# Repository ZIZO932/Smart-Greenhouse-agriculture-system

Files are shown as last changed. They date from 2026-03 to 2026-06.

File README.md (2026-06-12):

# Smart Greenhouse agriculture system
## Description
The Smart Greenhouse agriculture system uses a 4-layer design to protect crops like Basil from Egypt's heat and water shortages. A Raspberry Pi Pico W monitors industrial NPK and moisture sensors, then automatically triggers pumps and fans to keep everything in the perfect range. To top it off, an AI-powered camera on a circular track patrols the plants to catch diseases early.
---

## Why I Built This (The "Problem")
Farming in Egypt is genuinely getting harder. Water stress and heatwaves are a real problem, and sensitive crops like Basil and Stevia are expensive to lose. Most of the "smart farming" products I found were just monitors — they'd send you an alert saying the soil was dry, and that was it. You still had to go do something about it.
That gap is what pushed me to build this. I wanted a system that doesn't just report a problem, but fixes it. Nitrogen drops? The system pumps nitrogen. Temperature spikes? The fans come on. The whole point was to move from observation to actual automation.

---

## The 3D Model: A Three-Layer Stack
Final 3D Model

I designed this in a vertical configuration (inspired by city planning) to keep things clean and functional.

* **Layer 1 (The Pump Room):** This is the foundation. It holds a 5L main water tank for irrigation and three 1L tanks for N, P, and K nutrients. I mapped out four water pumps here, each hooked up to its own plumbing line.
* **Layer 2 (The Brain & Sensors):** This is where the electronics live. I installed industrial-grade NPK and moisture sensors here. The plumbing from the bottom passes through this layer to reach the top, which was a total nightmare to route without kinks.
* **Layer 3 (The Grow Bed):** I went with a transparent acrylic finish for the soil bed so you can actually see the root health. It uses 360-degree bubblers to make sure water reaches everywhere with zero waste.
* **The AI Track:** Encircling the top is a custom circular track. I built a small car that carries the Pi Zero and Camera, revolving around the plants every 30 minutes to catch every angle.

   **This is the link for the 3d model in step i didnt upload it here because of its size** https://drive.google.com/file/d/1caedlcHiUJ2DHqxGwvVZIDkTWpKjw0eq/view?usp=drive_link
  it is also found as a .zip file in the CAD folder

---

## Schematic & PCB Design
I spent a lot of time making sure this board wouldn't catch fire. Since the Pico is a low-power "brain," it can't handle the 12V needed for pumps and heaters.

### The Schematic
Schematic Design

The heart of the protection is the ULN2803A Darlington array. It acts as the mediator—taking tiny 3.3V signals from the Pico and using them to trigger the heavy-duty relays. I also built three distinct power rails to keep the noise down:
* **12V:** For the (pumps/fans/heaters).
* **5V:** For the MCUs (stepped down via LM2596T-5).
* **3.3V:** For the sensitive sensors (stepped down via AMS1117-3.3).

I added 560-ohm resistors and a MAX485E chip to handle the RS-485 Modbus communication with the NPK sensor. It’s industrial-grade stuff, not that cheap analog junk.

### The PCB
PCB Layout

I had to fix mistakes with relay footprints and ensure the power rails were wide enough to handle the current. I added decoupling capacitors everywhere to soak up voltage spikes from the pumps. After a few DRC (Design Rule Check), the board is officially intersection free and ready for production.

---

## AI Disease Detection
The patrol car sends images back to the Pi Zero 2W for processing. I'm training the disease detection model on the**[New Plant Diseases Dataset on Kaggle](https://www.kaggle.com/datasets/vipoooool/new-plant-diseases-dataset)**, which has a solid variety of labeled leaf conditions.
The workflow is simple: the car wakes up every 30 minutes, does one full lap around the plants scanning for spots or wilting, then returns to its dock to charge. Keeping it parked between scans was a deliberate choice to extend battery life.

---
## BOM

| Name | Cost Per Item (USD) | Quantity | Total (USD) | Link | Distributor |
| :--- | :--- | :--- | :--- | :--- | :--- |
| **Water pump** | 5.57 | 4 | 22.28 | [Link](https://www.ram-e-shop.com/shop/dc-pump-240l-water-pump12vdc-ultra-quiet-brushless-240l-h-7953) | Ram Electronics |
| **PCB Fabrication** | 5.74 | 1 | 5.74 | [Link](https://jlcpcb.com) | JLCPCB |
| **Pin Header 1x04** | 0.12 | 2 | 0.24 | [Link](https://makerselectronics.com/product/pin-headers-male-2-54mm-5pin-straight-black-11mm/) | Makers Electronics |
| **Pin Header 1x02** | 0.10 | 7 | 0.67 | [Link](https://makerselectronics.com/product/pin-headers-male-2-54mm-5pin-straight-black-11mm/) | Makers Electronics |
| **Ceramic Cap** | 0.04 | 10 | 0.38 | [Link](https://makerselectronics.com/product/ceramic-capacitor-100nf-50v/) | Makers Electronics |
| **Electrolytic Cap** | 0.10 | 4 | 0.40 | [Link](https://makerselectronics.com/product/capacitor-10uf-25v-4x7mm/) | Makers Electronics |
| **Resistor** | 0.04 | 10 | 0.40 | [Link](https://makerselectronics.com/product/carbon-resistor-10k%cf%89-2w-through-hole/) | Makers Electronics |
| **12V 5A Power Adapter** | 5.74 | 1 | 5.74 | [Link](https://makerselectronics.com/product/adapter-12v-3a-3/) | Makers Electronics |
| **Barrel Jack** | 0.29 | 1 | 0.29 | [Link](https://store.fut-electronics.com/products/dc-barrel-female-jack?_pos=2&_sid=9cbb68bec&_ss=r) | Future Electronics Egypt |
| **DIP-18 Socket** | 3.16 | 1 | 3.16 | [Link](https://store.fut-electronics.com/search?type=product&q=DIP-18+7.62mm) | Future Electronics Egypt |
| **Relay** | 1.34 | 7 | 9.38 | [Link](https://www.amazon.eg/-/en/Generic-12V-Relay-SRD-12VDC-SL-C-Automatic/dp/B09GNYCBJ8) | Amazon Egypt |
| **Schottky Diode** | 0.15 | 1 | 0.15 | [Link](https://store.fut-electronics.com/products/copy-of-diode-1n5408-3a-1000v-high-current-rectifier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) | Future Electronics Egypt |
| **Inductor** | 0.02 | 1 | 0.02 | [Link](https://makerselectronics.com/product/inductor-330uh-0510-1w/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) | Makers Electronics Egypt |
| **NPK Soil Sensor** | 61.26 | 1 | 61.26 | [Link](https://store.fut-electronics.com/products/soil-npk-nitrogen-phosphorus-potassium-nutrient-sensor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) | Future Electronics Egypt |
| **Soil Moisture Sensor** | 1.91 | 1 | 1.91 | [Link](https://www.ram-e-shop.com/shop/sen-soil-c-capacitive-analog-soil-moisture-sensor-v2-0-sku-soil-c-8116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) | RAM Electronics |
| **Light Sensor** | 3.73 | 1 | 3.73 | [Link](https://store.fut-electronics.com/products/digital-light-intensity-module) | Future Electronics Egypt |
| **Temp Sensor (air)** | 0.86 | 1 | 0.86 | [Link](https://makerselectronics.com/product/ds18b20-temperature-sensor-to-92/) | Makers Electronics Egypt |
| **Temp Sensor (soil)** | 1.63 | 1 | 1.63 | [Link](https://www.ram-e-shop.com/ar/shop/wire-ds18b20-ds18b20-waterproof-temperature-sensor-original-chip-7175) | RAM Electronics |
| **Darlington Driver** | 0.46 | 1 | 0.46 | [Link](https://makerselectronics.com/product/uln2803apg-darlington-transistor-arrays-dip-18-brand-toshiba/) | Makers Electronics |
| **RS485 Transceiver** | 0.55 | 1 | 0.55 | [Link](https://uge-one.com/product/max485-rs-485-transceiver-dip8/) | UGE Electronics Egypt |
| **Raspberry Pi Camera V2** | 15.31 | 1 | 15.31 | [Link](https://www.ram-e-shop.com/ar/shop/rpi-v2-camera-raspberry-pi-camera-module-v2-official-8-mp-hd-imx219-official-6887) | Ram Electronics |
| **LDO Regulator** | 0.06 | 1 | 0.06 | [Link](https://www.ram-e-shop.com/ar/shop/lt1117-3-3v-ams1117-3-3v-6628) | Ram Electronics Egypt |
| **Buck Converter IC** | 0.77 | 1 | 0.77 | [Link](https://makerselectronics.com/product/lm2596t-5-0-buck-fixed-40v-5v-3a-to-220-5l-dc-dc-converters-dip-ic/) | Makers Electronics Egypt |
| **Raspberry Pi Zero 2W** | 38.28 | 1 | 38.28 | [Link](https://devboardsmarket.com/products/raspberry-pi-zero-2-w) | DEV boards |
| **Raspberry Pi Pico W** | 16.27 | 1 | 16.27 | [Link](https://www.ram-e-shop.com/ar/shop/rpi-pico-w-raspberry-pi-pico-w-wifi-8524) | RAM electronics |
| **GRAND TOTAL** | | | **$189.94** | | |

## The Build: From CAD to Reality

After the design got approved, it was time to build the prototype — and as always, the real world had different plans than the 3D model.



The body is built from MDF wood with a polyethylene cover for the grow layer. First attempt used nails, which couldn't hold the weight and the frame fell apart — switched to screws and it held solid after that. Pumps and tubing were routed through the layers down to the soil bed.

Circuit

For the circuit, I soldered up the power supply (3.3V/5V step-downs, 10A fuse), wired in the sensors (BH1750, DS18B20, NPK via RS-485/MAX485) and the relay module driving the pumps, fans, Peltier module, and LEDs. Fried a Pico along the way and switched to an ESP32.

Dashboard

Real-time data flows through MQTT (Mosquitto) into a web dashboard built with HTML/CSS/JS and Grafana, showing live sensor readings against the ideal ranges for sweet basil.

Ran a full 6-hour test with everything powered on together — sensors reading correctly, pumps responding properly, and all values staying within range. The Smart Greenhouse Agriculture System is built and working. 🌱

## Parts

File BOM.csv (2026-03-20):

Name | Purpose | Cost Per Item (USD) | Quantity | Total (USD) | Link | Distributor
Water pump | to pump water and solution to irrigate the soil and plant | 5.57 | 4 | 22.28 | https://www.ram-e-shop.com/shop/dc-pump-240l-water-pump12vdc-ultra-quiet-brushless-240l-h-7953 | Ram Electronics
PCB Fabrication | to mount components | 5.74 | 1 | 5.74 | https://jlcpcb.com | JLCPCB
Pin Header 1x04 | To connect pico with zero | 0.12 | 2 | 0.24 | https://makerselectronics.com/product/pin-headers-male-2-54mm-5pin-straight-black-11mm/ | Makers Electronics
Pin Header 1x02 | To connect pico with zero | 0.10 | 7 | 0.67 | https://makerselectronics.com/product/pin-headers-male-2-54mm-5pin-straight-black-11mm/ | Makers Electronics
Ceramic Cap | circuit | 0.04 | 10 | 0.38 | https://makerselectronics.com/product/ceramic-capacitor-100nf-50v/ | Makers Electronics
Electrolytic Cap | circuit | 0.10 | 4 | 0.40 | https://makerselectronics.com/product/capacitor-10uf-25v-4x7mm/ | Makers Electronics
Resistor | For the circuit | 0.04 | 10 | 0.40 | https://makerselectronics.com/product/carbon-resistor-10k%cf%89-2w-through-hole/ | Makers Electronics
12V 5A Power Adapter | to power the whole system | 5.74 | 1 | 5.74 | https://makerselectronics.com/product/adapter-12v-3a-3/ | Makers Electronics
Barrel Jack | to plug in the 12V power supply | 0.29 | 1 | 0.29 | https://store.fut-electronics.com/products/dc-barrel-female-jack?_pos=2&_sid=9cbb68bec&_ss=r | Future Electronics Egypt
DIP-18 Socket | Holds the ULN2803A chip so you can replace it easily | 3.16 | 1 | 3.16 | https://store.fut-electronics.com/search?type=product&q=DIP-18+7.62mm | Future Electronics Egypt
Relay | switches that allow the Pico (low power) to turn on the Water Pumps, Fan, and Heater (high power) | 1.34 | 7 | 9.38 | https://www.amazon.eg/-/en/Generic-12V-Relay-SRD-12VDC-SL-C-Automatic/dp/B09GNYCBJ8 | Amazon Egypt
Schottky Diode | parts of the buck converter circuit | 0.15 | 1 | 0.15 | https://store.fut-electronics.com/products/copy-of-diode-1n5408-3a-1000v-high-current-rectifier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 | Future Electronics Egypt
Inductor | parts of the buck converter circuit | 0.02 | 1 | 0.02 | https://makerselectronics.com/product/inductor-330uh-0510-1w/ | Makers Electronics Egypt
NPK Soil Sensor | To monitor the NPK in soil (nitrogen, phosphorus, potassium) | 61.26 | 1 | 61.26 | https://store.fut-electronics.com/products/soil-npk-nitrogen-phosphorus-potassium-nutrient-sensor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 | Future Electronics Egypt
Soil Moisture Sensor | To monitor the soil moisture | 1.91 | 1 | 1.91 | https://www.ram-e-shop.com/shop/sen-soil-c-capacitive-analog-soil-moisture-sensor-v2-0-sku-soil-c-8116 | RAM Electronics
Light Sensor | To monitor the light intensity | 3.73 | 1 | 3.73 | https://store.fut-electronics.com/products/digital-light-intensity-module | Future Electronics Egypt
Temp Sensor (air) | To monitor the temp of air in the greenhouse system | 0.86 | 1 | 0.86 | https://makerselectronics.com/product/ds18b20-temperature-sensor-to-92/ | Makers Electronics Egypt
Temp Sensor (soil) | To monitor the temp of soil | 1.63 | 1 | 1.63 | https://www.ram-e-shop.com/ar/shop/wire-ds18b20-ds18b20-waterproof-temperature-sensor-original-chip-7175 | RAM Electronics
Darlington Driver | lets the Pico's tiny signal actually trigger the heavy coils inside the relays | 0.46 | 1 | 0.46 | https://makerselectronics.com/product/uln2803apg-darlington-transistor-arrays-dip-18-brand-toshiba/ | Makers Electronics
RS485 Transceiver | Translates the industrial signal from the NPK sensor into a language the Pico | 0.55 | 1 | 0.55 | https://uge-one.com/product/max485-rs-485-transceiver-dip8/ | UGE Electronics Egypt
Raspberry Pi Camera Module V2 | The eyes for the Pi Zero for ai. | 15.31 | 1 | 15.31 | https://www.ram-e-shop.com/ar/shop/rpi-v2-camera-raspberry-pi-camera-module-v2-official-8-mp-hd-imx219-official-6887 | Ram Electronics
LDO Regulator | power regulates down the voltage to a 3.3V rail | 0.06 | 1 | 0.06 | https://www.ram-e-shop.com/ar/shop/lt1117-3-3v-ams1117-3-3v-6628 | Ram Electronics Egypt
Buck Converter IC | To step down the voltage. | 0.77 | 1 | 0.77 | https://makerselectronics.com/product/lm2596t-5-0-buck-fixed-40v-5v-3a-to-220-5l-dc-dc-converters-dip-ic/ | Makers Electronics Egypt
Raspberry Pi Zero 2W | It would be used in the AI disease detection using pi camera | 38.28 | 1 | 38.28 | https://devboardsmarket.com/products/raspberry-pi-zero-2-w | DEV boards
Raspberry Pi Pico W | The main controller for the sensors and actuators | 16.27 | 1 | 16.27 | https://www.ram-e-shop.com/ar/shop/rpi-pico-w-raspberry-pi-pico-w-wifi-8524 | RAM electronics

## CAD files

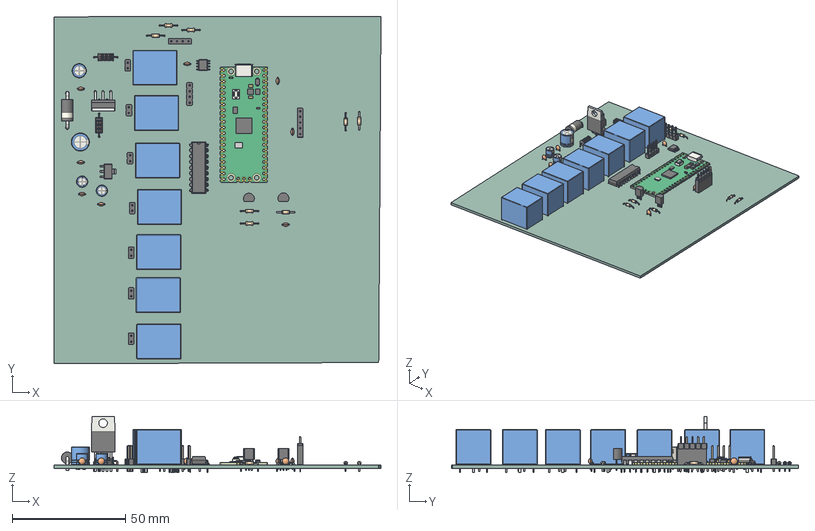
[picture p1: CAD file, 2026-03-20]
CAD/cap 204.step
144.5 x 153.5 x 24.8 mm
C_Disc_D3.0mm_W1.6mm_P2.50mm x 8
R_Axial_DIN0204_L3.6mm_D1.6mm_P7.62mm_Horizontal x 8
D_DO-201AD_P15.24mm_Horizontal
Relay_SPDT_SANYOU_SRD_Series_Form_C x 7
PinHeader_1x05_P2.54mm_Vertical
PinSocket_1x05_P2.54mm_Vertical
SOIC-8_3.9x4.9mm_P1.27mm
PinHeader_1x02_P2.54mm_Vertical x 7
RaspberryPi_Pico_Module_KiCad
SOT-223
TO-92_Inline x 2
PinHeader_1x04_P2.54mm_Vertical x 2
L_Axial_L7.0mm_D3.3mm_P10.16mm_Horizontal_Fastron_MICC x 2
CP_Radial_D5.0mm_P2.50mm x 2
CP_Radial_D6.3mm_P2.50mm
TO-220-5_P3.4x3.7mm_StaggerOdd_Lead3.8mm_Vertical
DIP-18_W7.62mm
CP_Radial_D8.0mm_P3.50mm
cap 204_PCB

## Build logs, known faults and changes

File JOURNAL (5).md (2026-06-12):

<!--
  This journal is auto generated by Stasis.
-->

# 6/12/2026 6 PM - Final Day

_Time spent: 6h_

Today was the final push. I mounted the ESP32 and the relay module inside the electronics layer and connected everything back to the circuit I had built in the first four days. I also attached the LED strip to the inner roof and mounted the Peltier module and fan on the upper wall. After everything was physically in place I powered it on for the first time as a complete system and it actually worked which was a relief. The sensors were reading correctly and the pumps were responding to the relay signals. I ran a quick test by letting it run for a couple hours while I watched the readings on the webpage and everything stayed in range. The prototype is done. And i did a full test plan video in which it worked for full 6 hours.

image (2)

image (1)




# 6/12/2026 6 PM - Construction Day 2 Prototype fix

_Time spent: 5h_

Today was probably the worst day so far. When I was moving the prototype to test the fit of the layers, the whole thing basically fell apart because the nails couldn't handle the weight. I had to stop everything and rethink the joining method. I replaced all the nails with screws which required drilling holes first which took a lot of time but the structure became way more solid after that. I also started mounting the pumps on the top layer and routing the silicone tubing down through the layers to the soil bed. Getting the tubes to go through without kinking was a pain but I figured it out by the end.











# 6/12/2026 6 PM - Construction Day 1

_Time spent: 4h_

Today I started the actual construction of the body. I began by cutting the MDF wood into the right dimensions for the walls and the layers. It took more time than I expected since I had to measure everything twice to make sure the layers would actually line up. After cutting, I started assembling the frame using nails and wood glue to hold everything together. It looked solid at first but I had a feeling the nails weren't going to hold for long since the wood pieces were pretty heavy. I also cut the polyethylene sheet and attached it to the upper layer to act as the greenhouse cover. Getting it tight and wrinkle free was annoying but I managed. At the end of the day the basic skeleton of the prototype was standing which felt good.











# 6/12/2026 6 PM - Website

_Time spent: 4h_

Today, I began making my webpage. I used the Grafana JS library, and I used basic HTML, CSS, and JS. I wrote the code to illustrate a real-time graph from phpMyAdmin. And I wrote the perfect conditions for our plant, which is sweet basil. Also, I made its style like our poster for the project, and I made it read the signals from the ESP using Wi-Fi, and I took a lot of time to make it. Since there were some mistakes in the code, like a bad connection or bad signal, I took some time to figure it out, but I corrected the code, and it worked at the end.

web_1

web_2

web_3





# 6/12/2026 6 PM - ESP Server

_Time spent: 5h_

Today, I wanted to make a server to provide the readings and the real-time graphs to my website, which I will build. I began by searching for popular protocols that can be used with the ESP32. I found that the best IoT-based protocol is MQTT. I installed Mosquitto, which is a really fast and reliable server to host my client. I had some problems when I was using it, so I began researching, and I changed some lines in mosquitto.config. Also, I installed XAMPP to serve my web page on the World Wide Web and to be the main server to run Apache and MySQL, and I wrote Python code to connect my ESP32 signals with Grafana from my web page to display real-time graphs. This is the code I wrote [python 1, python 2 images]. Also, I wrote an MQTT code to test my prototype as shown in these images [mqtt 1, mqtt 2].

python_1

python_2

mqtt_1

mqtt_2






# 6/12/2026 6 PM - Circuit Day 2

_Time spent: 3h_

On day two I began by wiring up the relay, ESP32, temp sensor (DS18B20), and light sensor (BH1750) and began connecting the RS485 NPK sensor. Also, I connected the MAX485 to be the main translator between the ESP32 and the NPK sensor. It took some time since it needed a 4800 baud rate and needed 12 volts, so I wired the power supply too, and the NPK sensor was hard to code, and I took like an hour to make it work.
Until now, I didn’t check the capacitors of all the sensors and some of the actuators since I had a deadline and exams in school. So I remade their systems again, but a lot faster now, and all worked by a simple code that was testing everything on its own. Then when I connected all of them, there was an overload on the step-down LM35, which was burnt. Also, I didn’t begin in the logic till now, but the light sensor was not working properly and had many wrong measures, and then I rewired the connections and reuploaded the code; it worked.











# 6/12/2026 6 PM - Circuit Day 1

_Time spent: 6h_

On day one, I started working on the circuit; I reviewed the schematic and confirmed that all the components I had purchased were present. Then I began by soldering the Pico. Then I soldered some more components. After that, I began connecting the power supply and the switch, which was the essential part for the project since it is the main power source as shown in this image. It took me some time to figure out that we needed a 10 amp fuse, so we got it, and it worked, and we measured it using a multimeter. After that, I connected the circuit of the power supply to reduce noise, and I connected the AMS1117 and LM25, which are step-downs, one for 3.3 volts and the other for 5 volts.
After that we got the breadboard and added the Pico to it. Then I connected the Pico with 5V from the power supply, so I fried it literally. I had an old ESP32, and when we checked, we used it instead of the Pico and connected it correctly with the power supply using a step-down, obviously. Then I began connecting the components into the breadboard. I connected the DS18B20 temp sensor and the BH1750, but I had a problem with the BH1750, which was that I connected it with the power supply, and I figured out that it should be connected to the 3.3V from the ESP32. It took me like 15 minutes to figure that out.
I began connecting the relay module, and I had trouble knowing if it was high-based or low-based, which makes the code different, so I know it is high-based, and also I began connecting the actuators like the water pumps, fans, Peltier module, and LEDs. At first it didn’t work at all since I was connecting it to 5 volts instead of 12 volts, so I reconnected it, and I made sure that everything was working and the signals were correctly matching the channels of the relay module.
WhatsApp Image 2026-04-19 at 2.10.47 PM






# 3/19/2026 12 PM - Building the Firmware last day

_Time spent: 3h_

Today I worked on the Pi Zero communication code, using UTF-8 to make sure everything reads correctly and keeping it all in JSON format so the data stays organized. I also built an NPK alert system to catch any big nutrient problems before they cause damage. After that, I added the specific functions for the water pumps, fans, and heaters to control them based on what the sensors are actually seeing. I made sure to include an emergency function too, just so I have a quick way to shut down all the actuators at once if something goes wrong.

This was the last day for the firmware since I finally got into the main.py file. I started with a simple welcome message and declared all my variables. The main while loop is now running—it reads through the sensors one by one, checks the Pi Zero connection, and sends the data over. I added a 500ms delay at the end to keep the timing stable. To wrap things up, I made a keyboard interrupt function so I can kill the whole process and close every relay instantly if I need to stop the system manually.






















# 3/18/2026 12 PM - Building the Firmware 1

_Time spent: 4h_

This was the firs day in which I started on the firmware for the project. I began by setting up the optimal values for the Basil plants, putting all the min and max parameters into one class. I also made a separate class to define what every pin on the Pico actually does so the code stays organized.

For the sensors, I started with the BH1750 light sensor. I wrote the code to check the I2C connection, handle the read delays, and then I used a formula I found to convert the raw data into actual light levels. Next, I worked on the NPK sensor, which has 7 registers. I built a function for it to self-read and return the soil nutrient data.

After the sensors, I moved on to the relays. I wrote functions to handle opening, closing, and timing for each one. For the temperature sensors, I used the OneWire library to scan the DS18B20 sensors. I set them to 12-bit conversion for better accuracy and added an "if" condition to sort the readings between soil and air temperature.

The moisture sensor was simpler since it just reads the data directly. Finally, I coded the light schedule to manage the plant's day/night cycles, which is pretty important for the photosynthesis and respiration process.

















# 3/17/2026 12 PM - AI Tracking System

_Time spent: 2h_

I finally got the physical model for the tracking system done. I designed a circular track that runs along the perimeter of the top layer to give the camera a full view of the plants. I also built a small car that sits on this track to carry the Raspberry Pi Zero 2W and the Pi Camera.

The idea is for the car to revolve around the growing area so it can catch every angle of the plants. I made sure the car is stable enough to hold the electronics and the battery pack while it moves. It took some time to get the curves of the track right so the car wouldn't get stuck, but it’s now a smooth loop. This setup is what will allow the AI to scan for diseases every 30 minutes before returning to its home position to save power.


















# 3/16/2026 12 PM - PCB Design and footprint

_Time spent: 5h_

Today, I began mapping my pcb design and preparing the footprints for the sensors and actuators. And I began with connecting each part like the RS485 sensors and capacitors and every sensors as a different system. Which take some time. I faces some problem which is the capacitors was different sizes and I didn't see that so I searched on every capacitor and its footprints.then by connecting the main power rails for every system and made sure every thing is connected without intersections. Also, I made sure to connect everything with it's rails. I connected the relays system and discovered I made a mistake in the footprints of the relays and I searched on the true ones and I made them and reconnected the relays systems. So, I ran a DRC check and found some errors like the silicon pring and the edge cuts. And some pins which is not allained with the schematic of the pi pico. So I got the true footprints and reconnected the system again and made made sure every thing is connected the right way and ran another DRC every thing was working.












# 3/15/2026 12 PM - High-Power Actuators with a Low-Power Brain

_Time spent: 4h_

Today was all about the "muscles" of the system, getting the ULN2803A Darlington array wired up. Think of it as the mediator between the Raspberry Pi Pico and the Relay Modules. Since the Pico is a low-power "brain," it doesn't have the strength to flip the heavy-duty switches (the relays) that control my water pumps, fans, and heaters. The ULN2803A acts as the driver that allows those tiny 3.3V signals to trigger the high-power actuators without blowing anything up.

I spent the rest of the day in a deep-focus wiring marathon, connecting the sensors to the Pico. This wasn't just plug-and-play; I had to add the specific capacitors and resistors for each sensor to keep the data lines clean and protected. The real puzzle was the pin mapping, I had to go through the datasheets one by one to make sure every sensor's specific protocol (like I2C or Analog) was matched to a compatible pin on the Pico. It was a lot of double-checking, but the core "control center" is finally wired and ready to talk to the environment.

















# 3/14/2026 12 PM - Bridging the Pico and the Pi Zero

_Time spent: 5h_

This phase of the schematic was all about the "handshake" between the different brains of the system. After spending yesterday hunting down the exact libraries and PCB footprints for my components, I finally got everything imported and verified. Today’s mission was power and communication: getting the Raspberry Pi Pico and the Pi Zero 2W wired up to the same power rails and linked together. Since the Pi Zero will be moving on that circular track around the plants (rather than sitting on the main board), I designed header pins into the schematic so I can easily plug it in via a ribbon cable or jumper wires.

The real technical hurdle was the RS-485 communication. I integrated a MAX485E to act as the translator between the Pico’s logic and the industrial NPK sensor. Since the sensor runs on 12V, I tapped into the high-voltage rail, but I had to be careful with the signal lines. I used 560-ohm resistors to bias the lines and manage the charge so it’s perfectly safe for the MAX485 and the Pico to handle.

I also threw in a dedicated decoupling capacitor for the MAX485 chip itself; it’s a small detail, but it’s there to soak up any voltage spikes or "kickback" when the power gets cut, ensuring I don’t fry my communication bridge. It’s starting to look like a real industrial controller now.

















# 3/13/2026 12 PM - Staring Schematic

_Time spent: 3h_

Today was all about diving into the schematic design, which turned out to be a lot more about "protection" than just making connections. After doing some digging, I realized that every MCU and IC is actually pretty fragile—they need specific capacitors and resistors just to survive voltage spikes or prevent short-circuit damage. It’s one of those things you don't think about until you realize a tiny spark could fry your whole project.

To keep things organized, I mapped out three distinct power rails: 12V for the heavy-duty actuators, 5V for the MCUs, and 3.3V for the more sensitive sensors. Having these rails makes the wiring way less of a headache. I’m using a single 12V adapter as the main heart of the system, then stepping it down using an LM2596T-5 for the 5V line and an AMS1117-3.3 for the 3.3V line.

I didn't want to take any chances with stability, so I added four capacitors to each regulator to smooth out the voltage and act as a tiny buffer if the power flickers. I also integrated an inductor with the LM2596 to cut down on energy loss and threw in a diode to make sure current doesn't accidentally flow backward and wreck the source. It’s a lot of extra components, but it’s the only way to make sure the "brain" of the system doesn't lose its mind the second a pump kicks in. 












# 3/12/2026 12 PM - AI disease detection

_Time spent: 3h_

I also came up with a pretty ambitious plan for an AI disease detection subsystem to sit right on top of everything. The idea is to have a Raspberry Pi Zero 2W and a Pi Camera Module mounted on a wheeled platform that actually travels along a circular track around the perimeter of the growing area in Layer 3. This way, instead of a static view, the camera revolves around the plants to catch every single angle from a consistent distance.

To keep it efficient, the plan is for the system to run on a 30-minute cycle: every half hour, the platform wakes up, completes a full loop to capture images of the plants, and then returns to its home position to power down the motors completely. It’s designed to be a totally independent circuit from the main monitoring board, but it will feed all its visual data into the same cloud. I haven't built the physical model for this part yet, but having the concept mapped out gives me a clear path for adding high-tech "eyes" to the setup later on. The first image shows raspberry pi zero 2w connected to pi camera. and for the second image i got it from a research that trained an ai model to detect diseases.












# 3/11/2026 12 PM - Layer 2 and 3

_Time spent: 5h_

It took some serious effort, but I finally finished the three-layer stack. After the pump layer was set, I moved on to the second level, which acts as the brain for the electronics and sensors. The real grind was making sure the pipes from the bottom pumps were actually routed and connected properly to the bubblers on top without any kinks. Once the plumbing was secure, I installed the NPK and moisture sensors into the second layer, carefully positioning them so they’d be fully submerged in the soil once the bed was filled.

For the final layer, I went with a transparent acrylic finish for the soil bed so I can actually see the root health and water flow from the outside. Getting all three layers to line up, pumps on the bottom, sensors in the middle, and soil on top, was a massive coordination task, but seeing it all stacked together with the bubblers in place makes the whole system feel real. These are some figures of the whole model till now.













# 3/10/2026 12 PM - Layer 1

_Time spent: 1.5h_

I started the 3D model by setting up Layer 1 and getting the plumbing foundation right. It actually took me quite a while just to track down the exact 3D models I needed to match my parts, but once I had them, I mapped out the base and installed the four water pumps. I connected each one to its own tank, one 5-liter main tank for irrigation and three 1-liter tanks for the N, P, and K nutrients, and made sure every pump was properly hooked up to its own pipe. It’s a clean setup, and now that the physical layout is finished, the first layer is officially ready. i attached two pictures of the model.












# 3/9/2026 12 PM - Actuators selection

_Time spent: 4h_

After the sensors selection i shifted my focus on the actuators. My goal was simple on paper but a nightmare in practice: build a dedicated correction system for every single parameter I’m monitoring.

For the soil, I mapped out a 5-liter main water tank with a water pump for basic irrigation. But the NPK part is where it got complicated; I decided to add three separate pumps to dose Nitrogen, Phosphorus, and Potassium independently based on what the sensors say. I also found that to irrigate with least loss in water i need a 360 degree bubbler which i found in multiple websites.

For the climate, I settled on a fan and a heater to lock the temperature between 25°C and 30°C, plus a high-output LED. 

With 4 sensors and 7 actuators, I needed a controller that could handle a lot of I/O. I chose the Raspberry Pi Pico W. I love the Pico for its speed, and the "W" version gives me the Wi-Fi I’ll eventually need for a real-time feedback dashboard. The struggle today was mapping the pins. I realized that the Pico’s 3.3V logic can't directly talk to 12V pumps or the RS-485 sensor.
In the first image it shows the bubbler i want to use where to irrigate the whole soil i needed 360 one that has high reach.
In the second image it shows the schematic of a smart greenhouse system in which i took the idea of using a pico. 












# 3/8/2026 12 PM - Solution parameters and sensors selection

_Time spent: 5h_

Today i struggled in choosing parameters in the end i chose : NPK, Temperature, Light, and Soil Moisture. I figured if I could actually control these variables, I could grow high-value stuff like Basil or Stevia basically anywhere. Once I had the plan, I needed the "eyes" of the system and that’s where the real headache started. I spent hours looking for soil sensors, only to realize most of the cheap ones are basically toys; they just give you a vague conductivity reading and can't tell Nitrogen from Potassium.
I finally found an industrial RS-485 Modbus RTU NPK sensor. It’s way more expensive, and I know the code is going to be a total nightmare compared to a simple analog sensor, but it actually gives me real data i wanted. I also grabbed a capacitive moisture sensor because I knew the standard resistive ones would just rust and die in the soil. At least now I know the hardware can actually handle the job. The first image shows the NPK sensor i chose where its a bit expensive compared to something like 7 in 1 sensor the problem is the accuracy in which i want to make sure that the plant wont die not just a theortical thingy.
The second image is an image of the module used to connect the NPK sensor to any microcontroller. The third image shows the moisture soil sensor that was chosen due to the covarge of its forks which prevents rust.


















# 3/7/2026 12 PM - The Problem and past solutions

_Time spent: 4h_

For the first day it was all about the "Problem Selection" phase for my Capstone. I can't just build something "cool" it has to solve a legitimate Egyptian challenge. I spent hours looking into the agricultural sector. Egypt is struggling with environmental instability and major water stress. High-value aromatic crops like **Basil and Stevia** are taking a hit because they are so sensitive to heatwaves and irregular irrigation.

The Struggle i faced when searching for solutions is that Most smart pots only monitor; they don't fix. I realized I needed a system that actually manioulate the environment.
The Solution i chose was A 4-layered vertical infrastructure. It mimics city planning in which (Water pumbs and tank - Electronics - Soil - Environment). The first image shows a figure that i found in this paper (Smart Greenhouse Automation
System) where they developed the system in layers to make it easy to bulid and modify.
In the second image i attached there was the process that the system works in.













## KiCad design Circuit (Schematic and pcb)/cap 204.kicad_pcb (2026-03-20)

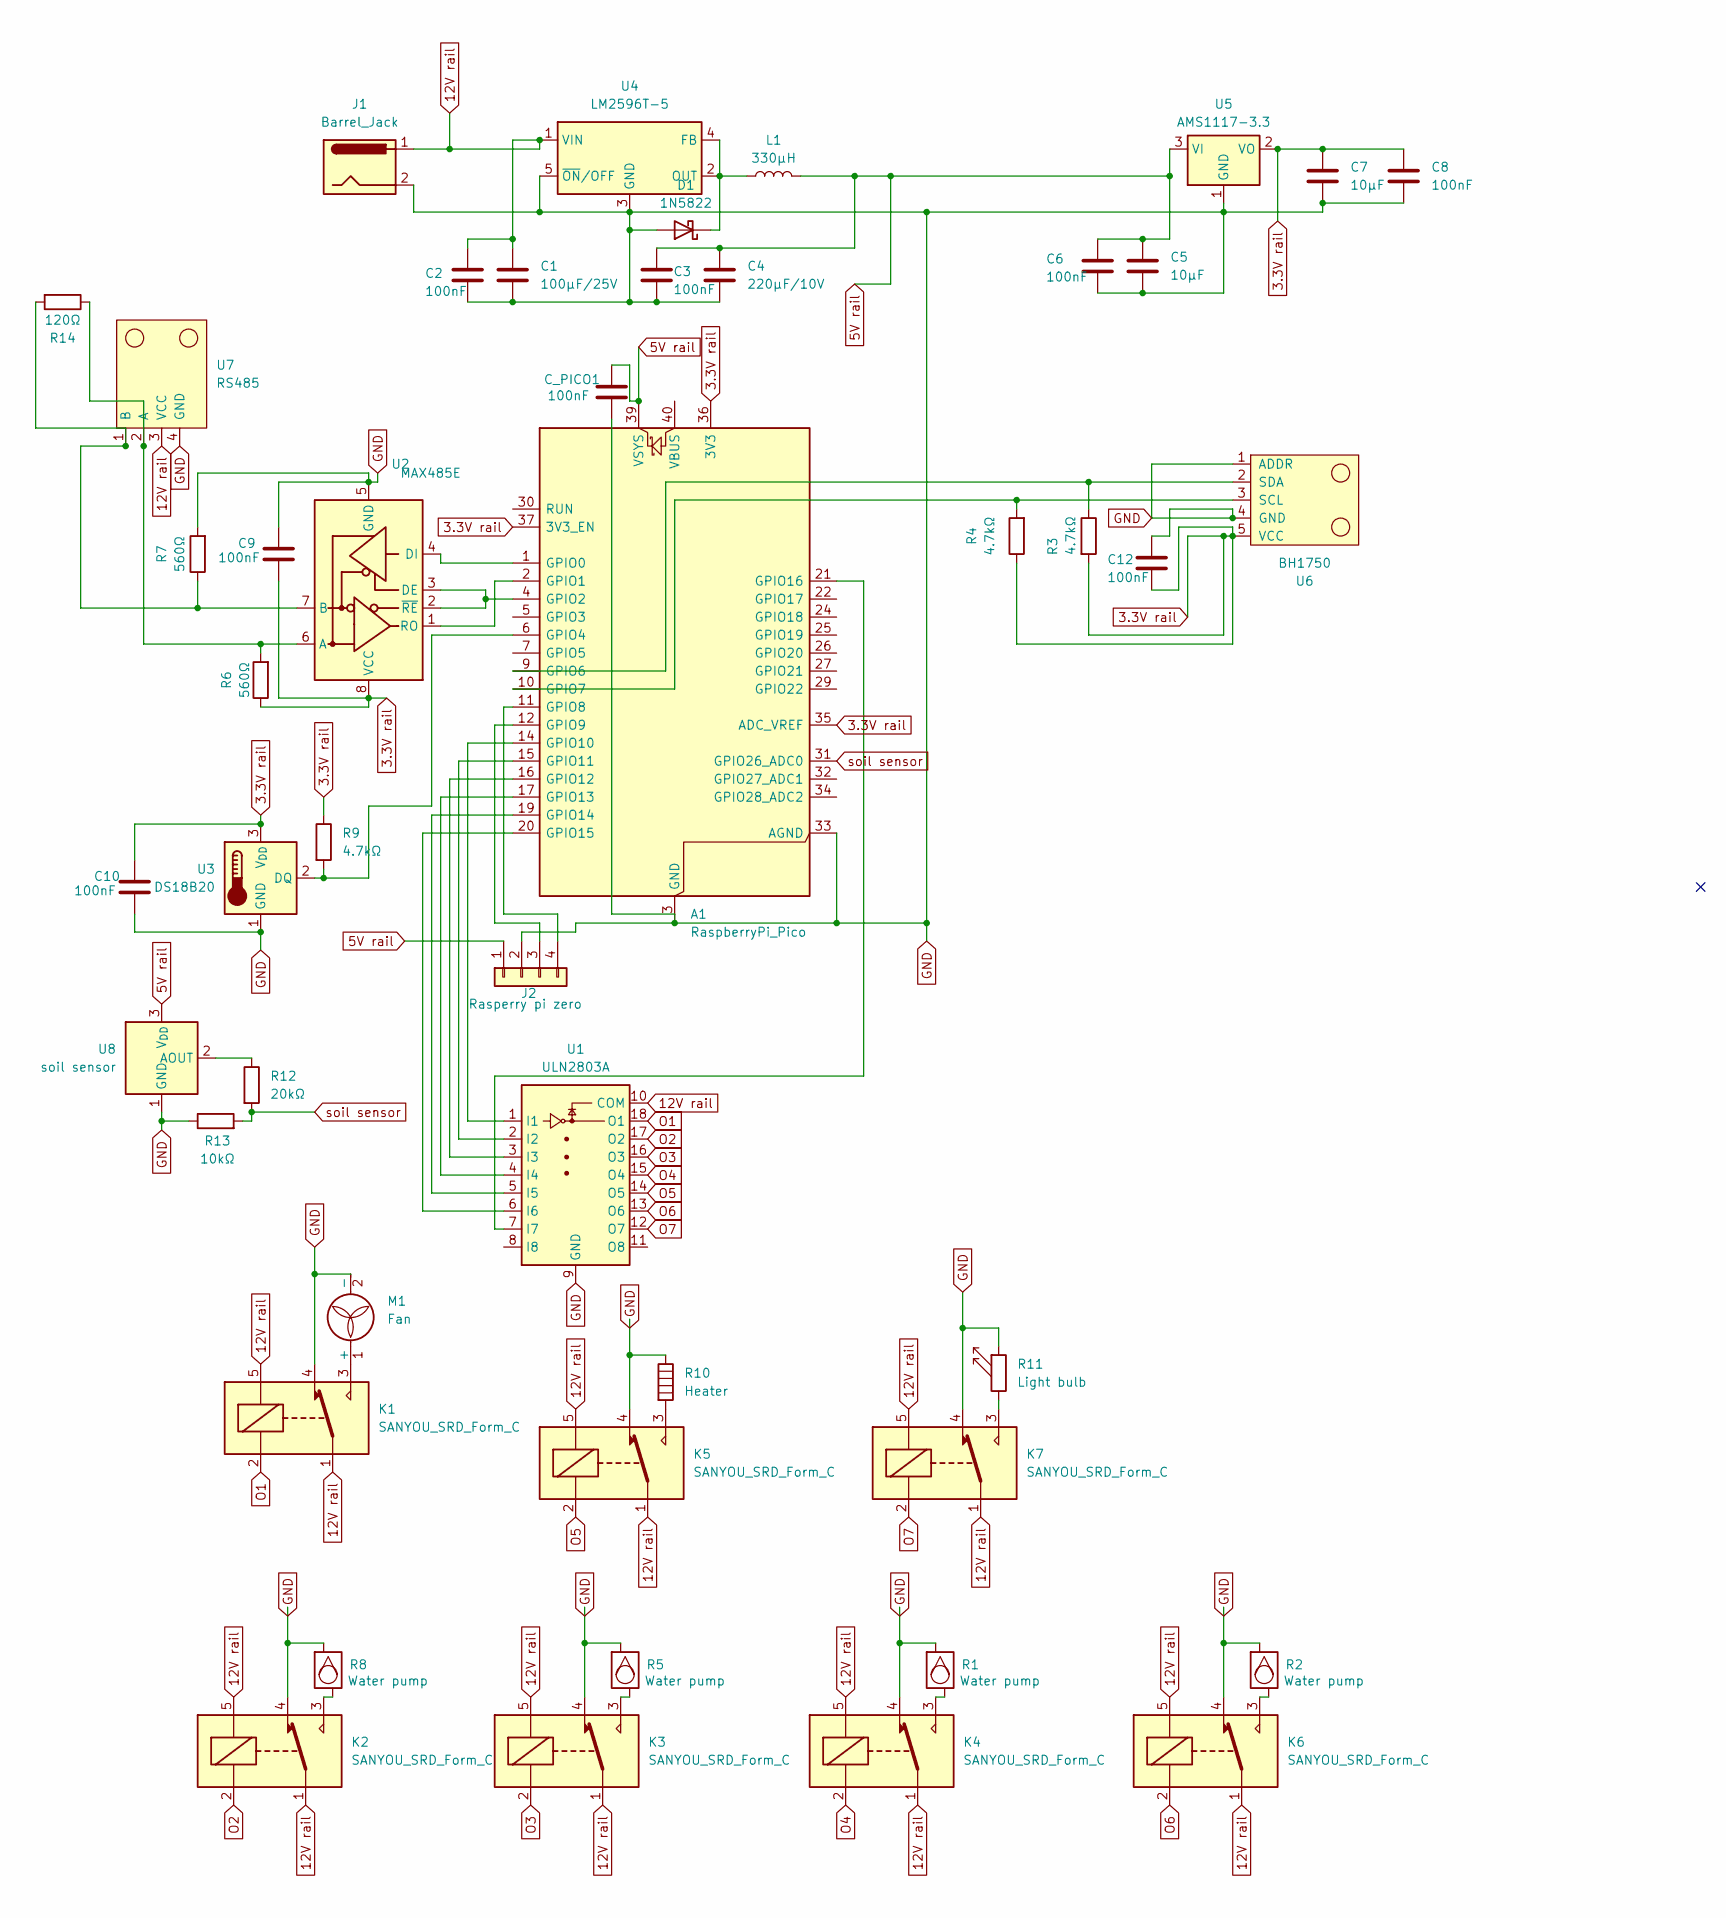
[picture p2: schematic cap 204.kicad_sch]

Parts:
A1: RaspberryPi_Pico; RaspberryPi_Pico_Common_Unspecified
C1: 100µF/25V; CP_Radial_D6.3mm_P2.50mm
C2, C3, C6, C8, C9, C10, C12: 100nF; C_Disc_D3.0mm_W1.6mm_P2.50mm
C4: 220µF/10V; CP_Radial_D8.0mm_P3.50mm
C5, C7: 10µF; CP_Radial_D5.0mm_P2.50mm
C_PICO1: 100nF; C_Disc_D3.0mm_W1.6mm_P2.50mm
D1: 1N5822; D_DO-201AD_P15.24mm_Horizontal
J1: Barrel_Jack; L_Axial_L7.0mm_D3.3mm_P10.16mm_Horizontal_Fastron_MICC
J2: Rasperry pi zero; PinHeader_1x04_P2.54mm_Vertical
K1, K2, K3, K4, K5, K6, K7: SANYOU_SRD_Form_C; Relay_SPDT_SANYOU_SRD_Series_Form_C
L1: 330µH; L_Axial_L7.0mm_D3.3mm_P10.16mm_Horizontal_Fastron_MICC
M1: Fan; PinHeader_1x02_P2.54mm_Vertical
R1, R2, R5, R8: Water pump; PinHeader_1x02_P2.54mm_Vertical
R3, R4, R9: 4.7kΩ; R_Axial_DIN0204_L3.6mm_D1.6mm_P7.62mm_Horizontal
R6, R7: 560Ω; R_Axial_DIN0204_L3.6mm_D1.6mm_P7.62mm_Horizontal
R10: Heater; PinHeader_1x02_P2.54mm_Vertical
R11: Light bulb; PinHeader_1x02_P2.54mm_Vertical
R12: 20kΩ; R_Axial_DIN0204_L3.6mm_D1.6mm_P7.62mm_Horizontal
R13: 10kΩ; R_Axial_DIN0204_L3.6mm_D1.6mm_P7.62mm_Horizontal
R14: 120Ω; R_Axial_DIN0204_L3.6mm_D1.6mm_P7.62mm_Horizontal
U1: ULN2803A; DIP-18_W7.62mm
U2: MAX485E; SOIC-8_3.9x4.9mm_P1.27mm
U3: DS18B20; TO-92_Inline
U4: LM2596T-5; TO-220-5_P3.4x3.7mm_StaggerOdd_Lead3.8mm_Vertical
U5: AMS1117-3.3; SOT-223-3_TabPin2
U6: BH1750; module_bh1750
U7: RS485; PinHeader_1x04_P2.54mm_Vertical
U8: soil sensor; TO-92_Inline

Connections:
3.3V rail: A1.35 (ADC_VREF), A1.36 (3V3), A1.37 (3V3_EN), C7.1, C8.1, C9.2, C10.1, C12.2, R3.2, R4.1, R6.1, R9.1, U2.8 (VCC), U3.3 (V_{DD}), U5.2 (VO), U6.5 (VCC)
5V rail: A1.39 (VSYS), C3.1, C4.1, C5.1, C6.1, C_PICO1.1, J2.1, L1.2, U5.3 (VI), U8.3 (V_{DD})
12V rail: C1.1, C2.1, J1.1, K1.1, K1.5, K2.1, K2.5, K3.1, K3.5, K4.1, K4.5, K5.1, K5.5, K6.1, K6.5, K7.1, K7.5, U1.10 (COM), U4.1 (VIN), U7.3 (VCC)
GND: A1.3 (GND), A1.8 (GND), A1.13 (GND), A1.18 (GND), A1.23 (GND), A1.28 (GND), A1.33 (AGND), A1.38 (GND), C1.2, C2.2, C3.2, C4.2, C5.2, C6.2, C7.2, C8.2, C9.1, C10.2, C12.1, C_PICO1.2, D1.2 (A), J1.2, J2.2, K1.4, K2.4, K3.4, K4.4, K5.4, K6.4, K7.4, M1.2 (-), R1.1, R2.1, R5.1, R7.2, R8.1, R10.1, R11.1, R13.1, U1.9 (GND), U2.5 (GND), U3.1 (GND), U4.3 (GND), U4.5 (~ON/OFF), U5.1 (GND), U6.1 (ADDR), U6.4 (GND), U7.4 (GND), U8.1 (GND)
unnamed: A1.1 (GPIO0), U2.4 (DI)
unnamed: A1.2 (GPIO1), U2.1 (RO)
unnamed: A1.4 (GPIO2), U2.2 (~RE), U2.3 (DE)
unnamed: A1.6 (GPIO4), R9.2, U3.2 (DQ)
unnamed: A1.9 (GPIO6), R3.1, U6.2 (SDA)
unnamed: A1.10 (GPIO7), R4.2, U6.3 (SCL)
unnamed: A1.11 (GPIO8), J2.4
unnamed: A1.12 (GPIO9), J2.3
unnamed: A1.14 (GPIO10), U1.1 (I1)
unnamed: A1.15 (GPIO11), U1.2 (I2)
unnamed: A1.16 (GPIO12), U1.3 (I3)
unnamed: A1.17 (GPIO13), U1.4 (I4)
unnamed: A1.19 (GPIO14), U1.5 (I5)
unnamed: A1.20 (GPIO15), U1.6 (I6)
unnamed: A1.21 (GPIO16), U1.7 (I7)
unnamed: D1.1 (K), L1.1, U4.2 (OUT), U4.4 (FB)
unnamed: K2.3, R8.2
unnamed: K3.3, R5.2
unnamed: K4.3, R1.2
unnamed: K5.3, R10.2
unnamed: K6.3, R2.2
unnamed: K7.3, R11.2
unnamed: K1.3, M1.1 (+)
unnamed: R6.2, R14.1, U2.6 (A), U7.2 (A)
unnamed: R7.1, R14.2, U2.7 (B), U7.1 (B)
unnamed: R12.1, U8.2 (AOUT)
O1: K1.2, U1.18 (O1)
O2: K2.2, U1.17 (O2)
O3: K3.2, U1.16 (O3)
O4: K4.2, U1.15 (O4)
O5: K5.2, U1.14 (O5)
O6: K6.2, U1.13 (O6)
O7: K7.2, U1.12 (O7)
soil sensor: A1.31 (GPIO26_ADC0), R12.2, R13.2

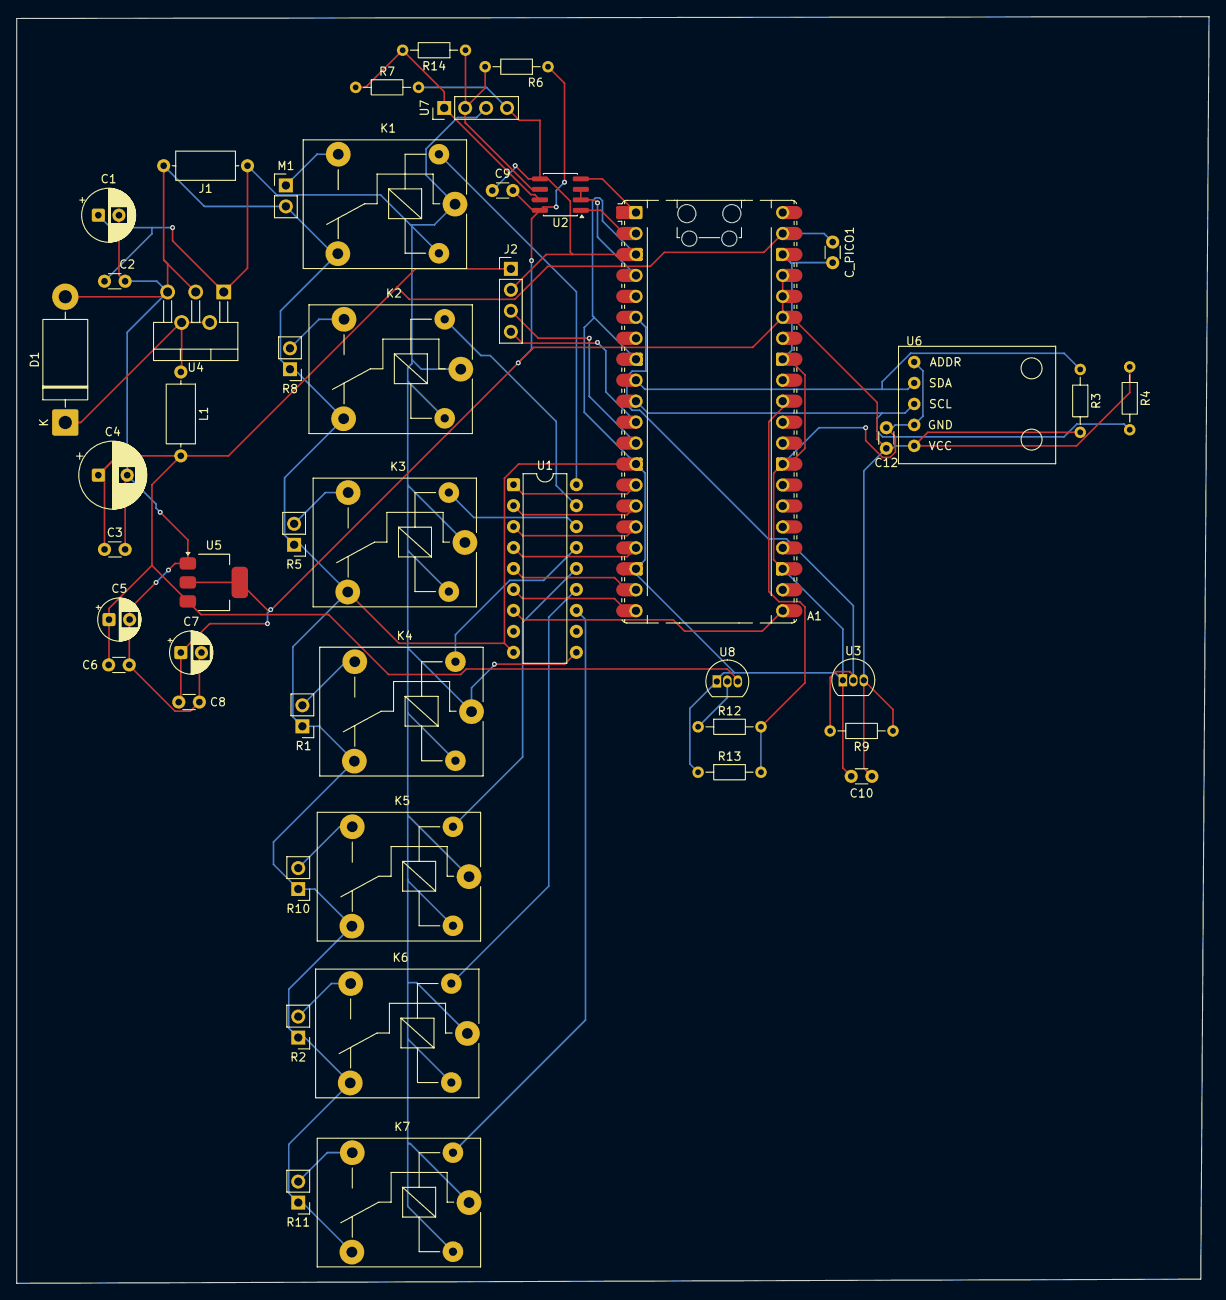
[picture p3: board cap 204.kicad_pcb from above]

Board: 2 copper layers, 144.5 x 153.5 mm, 47 parts (0 on the bottom side), 38 nets.

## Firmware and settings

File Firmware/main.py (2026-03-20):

import machine
from utime import sleep_ms, time
import onewire
import ds18x20
import struct
import json
from machine import Pin, ADC, I2C, UART


class BasilParams:
    TEMP_AIR_MIN        = 18.0
    TEMP_AIR_OPTIMAL    = 24.0
    TEMP_AIR_MAX        = 29.0
    TEMP_AIR_CRITICAL   = 35.0
    MOISTURE_MIN        = 55.0
    MOISTURE_TARGET     = 65.0
    MOISTURE_MAX        = 75.0
    LIGHT_MIN_LUX       = 15000
    LIGHT_MAX_LUX       = 50000
    LIGHT_ON_HOUR       = 6
    LIGHT_OFF_HOUR      = 22
    NITROGEN_MIN        = 120
    NITROGEN_MAX        = 200
    PHOSPHORUS_MIN      = 50
    PHOSPHORUS_MAX      = 100
    POTASSIUM_MIN       = 120
    POTASSIUM_MAX       = 200
    PUMP_MAX_ON_SEC     = 30
    PUMP_COOLDOWN_SEC   = 300
    WATERING_HOUR_START = 6
    WATERING_HOUR_END   = 20
    FAN_MIN_ON_SEC      = 10
    HEATER_MAX_ON_SEC   = 120
    HEATER_COOLDOWN_SEC = 60


class Pins:
    RS485_TX    = 0
    RS485_RX    = 1
    RS485_DE_RE = 2
    ONEWIRE     = 4
    I2C_SDA     = 6
    I2C_SCL     = 7
    MOISTURE    = 26
    PIZERO_TX   = 8
    PIZERO_RX   = 9
    PUMP_1      = 10
    PUMP_2      = 11
    PUMP_3      = 12
    PUMP_4      = 13
    FAN         = 14
    HEATER      = 15
    GROW_LIGHT  = 16


MOISTURE_DRY_RAW = 52000
MOISTURE_WET_RAW = 19000


class BH1750:
    ADDR          = 0x23
    CMD_CONT_HIGH = 0x10

    def __init__(self, i2c):
        self.i2c = i2c
        self.i2c.writeto(self.ADDR, bytes([self.CMD_CONT_HIGH]))
        sleep_ms(200)

    def read_lux(self):
        try:
            data = self.i2c.readfrom(self.ADDR, 2)
            raw = (data[0] << 8) | data[1]
            return raw / 1.2
        except:
            return -1


class NPKSensor:
    QUERY = bytes([0x01, 0x03, 0x00, 0x00, 0x00, 0x07, 0x04, 0x08])

    def __init__(self, uart, de_re_pin):
        self.uart  = uart
        self.de_re = de_re_pin

    def _crc16(self, data):
        crc = 0xFFFF
        for byte in data:
            crc ^= byte
            for _ in range(8):
                crc = (crc >> 1) ^ 0xA001 if crc & 0x0001 else crc >> 1
        return crc

    def read(self):
        self.de_re.value(1)
        sleep_ms(2)
        self.uart.write(self.QUERY)
        sleep_ms(10)
        self.de_re.value(0)
        sleep_ms(500)
        if self.uart.any() >= 19:
            raw = self.uart.read(19)
            if self._crc16(raw[:17]) != ((raw[18] << 8) | raw[17]):
                return None
            def reg(i):
                return (raw[3 + i*2] << 8) | raw[4 + i*2]
            return {
                "moisture_pct" : reg(0) / 10.0,
                "temp_c"       : reg(1) / 10.0,
                "ec_us_cm"     : reg(2),
                "ph"           : reg(3) / 10.0,
                "nitrogen"     : reg(4),
                "phosphorus"   : reg(5),
                "potassium"    : reg(6),
            }
        return None


class Relay:
    def __init__(self, pin_num, active_high=True):
        self.pin         = Pin(pin_num, Pin.OUT)
        self.active_high = active_high
        self.state       = False
        self.on_since    = 0
        self.off_since   = time()
        self.off()

    def on(self):
        self.pin.value(1 if self.active_high else 0)
        if not self.state:
            self.on_since = time()
        self.state = True

    def off(self):
        self.pin.value(0 if self.active_high else 1)
        if self.state:
            self.off_since = time()
        self.state = False

    def on_duration(self):
        return (time() - self.on_since) if self.state else 0

    def off_duration(self):
        return (time() - self.off_since) if not self.state else 0


class TempSensors:
    def __init__(self, pin_num):
        self.ow   = onewire.OneWire(Pin(pin_num))
        self.ds   = ds18x20.DS18X20(self.ow)
        self.roms = self.ds.scan()

    def read_air(self):
        try:
            self.ds.convert_temp()
            sleep_ms(800)
            return self.ds.read_temp(self.roms[0]) if self.roms else None
        except:
            return None


def read_moisture_pct(adc):
    raw = adc.read_u16()
    pct = (MOISTURE_DRY_RAW - raw) / (MOISTURE_DRY_RAW - MOISTURE_WET_RAW) * 100.0
    return max(0.0, min(100.0, pct))


class LightScheduler:
    def __init__(self):
        self.current_hour = 6
        self.synced       = False

    def update_hour(self, hour):
        self.current_hour = hour
        self.synced       = True

    def should_light_be_on(self, lux):
        p = BasilParams
        return (p.LIGHT_ON_HOUR <= self.current_hour < p.LIGHT_OFF_HOUR
                and lux < p.LIGHT_MIN_LUX
                and lux < p.LIGHT_MAX_LUX)


class PiZeroComm:
    def __init__(self):
        self.uart = UART(1, baudrate=115200,
                         tx=Pin(Pins.PIZERO_TX),
                         rx=Pin(Pins.PIZERO_RX),
                         timeout=50)
        self.buf = ""

    def send(self, data_dict):
        try:
            self.uart.write((json.dumps(data_dict) + "\n").encode())
        except:
            pass

    def receive(self):
        try:
            if self.uart.any():
                chunk = self.uart.read(256)
                if chunk:
                    self.buf += chunk.decode("utf-8", "ignore")
                    if "\n" in self.buf:
                        line, self.buf = self.buf.split("\n", 1)
                        return json.loads(line.strip())
        except:
            self.buf = ""
        return None


def check_npk_alerts(npk):
    if not npk:
        return []
    p      = BasilParams
    alerts = []
    if npk["nitrogen"]   < p.NITROGEN_MIN:   alerts.append(f"LOW_N:{npk['nitrogen']}")
    if npk["phosphorus"] < p.PHOSPHORUS_MIN: alerts.append(f"LOW_P:{npk['phosphorus']}")
    if npk["potassium"]  < p.POTASSIUM_MIN:  alerts.append(f"LOW_K:{npk['potassium']}")
    if npk["nitrogen"]   > p.NITROGEN_MAX:   alerts.append(f"HIGH_N:{npk['nitrogen']}")
    return alerts


def control_fan(fan_relay, temp_air):
    p = BasilParams
    if temp_air is None:
        return
    if temp_air >= p.TEMP_AIR_MAX:
        fan_relay.on()
    elif temp_air < p.TEMP_AIR_OPTIMAL - 1.0:
        if fan_relay.state and fan_relay.on_duration() >= p.FAN_MIN_ON_SEC:
            fan_relay.off()


def control_heater(heater_relay, temp_air):
    p = BasilParams
    if temp_air is None:
        return
    if heater_relay.state and heater_relay.on_duration() >= p.HEATER_MAX_ON_SEC:
        heater_relay.off()
        return
    if not heater_relay.state and heater_relay.off_duration() < p.HEATER_COOLDOWN_SEC:
        return
    if temp_air < p.TEMP_AIR_MIN:
        heater_relay.on()
    elif temp_air >= p.TEMP_AIR_OPTIMAL:
        heater_relay.off()


def control_pumps(pump_relays, moisture_pct, current_hour, last_pump_time):
    p   = BasilParams
    now = time()
    if not (p.WATERING_HOUR_START <= current_hour < p.WATERING_HOUR_END):
        for relay in pump_relays:
            relay.off()
        return last_pump_time
    if now - last_pump_time < p.PUMP_COOLDOWN_SEC:
        return last_pump_time
    for relay in pump_relays:
        if relay.state and relay.on_duration() >= p.PUMP_MAX_ON_SEC:
            relay.off()
    if moisture_pct < p.MOISTURE_MIN:
        if not pump_relays[0].state:
            pump_relays[0].on()
            return now
    elif moisture_pct >= p.MOISTURE_MAX:
        for relay in pump_relays:
            relay.off()
    return last_pump_time


def control_light(light_relay, lux, scheduler):
    if scheduler.should_light_be_on(lux) and not light_relay.state:
        light_relay.on()
    elif not scheduler.should_light_be_on(lux) and light_relay.state:
        light_relay.off()


def emergency_off(*relays):
    for r in relays:
        r.off()


def main():
    uart0 = UART(0, baudrate=9600,
                 tx=Pin(Pins.RS485_TX),
                 rx=Pin(Pins.RS485_RX),
                 timeout=600)
    de_re = Pin(Pins.RS485_DE_RE, Pin.OUT)
    de_re.value(0)
    npk_sensor = NPKSensor(uart0, de_re)

    i2c   = I2C(1, sda=Pin(Pins.I2C_SDA), scl=Pin(Pins.I2C_SCL), freq=400000)
    light = BH1750(i2c)
    temps = TempSensors(Pins.ONEWIRE)
    adc   = ADC(Pin(Pins.MOISTURE))

    pump1    = Relay(Pins.PUMP_1)
    pump2    = Relay(Pins.PUMP_2)
    pump3    = Relay(Pins.PUMP_3)
    fan      = Relay(Pins.FAN)
    heater   = Relay(Pins.HEATER)
    grow_led = Relay(Pins.GROW_LIGHT)
    pumps    = [pump1, pump2, pump3]

    pizero         = PiZeroComm()
    scheduler      = LightScheduler()
    last_pump_time = 0
    last_npk_time  = 0
    last_send_time = 0
    npk_data       = None

    while True:
        now          = time()
        air_c        = temps.read_air()
        lux          = light.read_lux()
        moisture_pct = read_moisture_pct(adc)

        if now - last_npk_time >= 60:
            npk_data      = npk_sensor.read()
            last_npk_time = now

        cmd = pizero.receive()
        if cmd:
            if "hour"       in cmd: scheduler.update_hour(cmd["hour"])
            if cmd.get("emergency_off"): emergency_off(pump1, pump2, pump3, fan, heater, grow_led)
            if "pump1"      in cmd: pump1.on()    if cmd["pump1"]      else pump1.off()
            if "grow_light" in cmd: grow_led.on() if cmd["grow_light"] else grow_led.off()

        if air_c is not None:
            control_fan(fan, air_c)
            control_heater(heater, air_c)

        if air_c and air_c >= BasilParams.TEMP_AIR_CRITICAL:
            fan.on()
            heater.off()

        last_pump_time = control_pumps(pumps, moisture_pct, scheduler.current_hour, last_pump_time)
        control_light(grow_led, lux, scheduler)

        if now - last_send_time >= 10:
            pizero.send({
                "t"        : now,
                "air_c"    : round(air_c, 2)       if air_c   else None,
                "lux"      : round(lux, 1)          if lux > 0 else None,
                "moisture" : round(moisture_pct, 1),
                "npk"      : npk_data,
                "alerts"   : check_npk_alerts(npk_data),
                "relays"   : {
                    "pump1"     : pump1.state,
                    "pump2"     : pump2.state,
                    "pump3"     : pump3.state,
                    "fan"       : fan.state,
                    "heater"    : heater.state,
                    "grow_light": grow_led.state,
                }
            })
            last_send_time = now

        sleep_ms(500)


if __name__ == "__main__":
    try:
        main()
    except KeyboardInterrupt:
        pass

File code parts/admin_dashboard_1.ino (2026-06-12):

#include <WiFi.h>
#include <PubSubClient.h>
#include <ArduinoJson.h>

// ===== WIFI =====
const char* ssid = "04_el_top";
const char* password = "Medo12345##";

// ===== MQTT =====
const char* mqtt_server = "192.168.0.169";
const int mqtt_port = 1883;

WiFiClient espClient;
PubSubClient client(espClient);

// ===== SENSOR ARRAYS =====
int tempArr[] = {20,21,22,23,24,25};
int lightArr[] = {100,200,300,400,500};
int moistArr[] = {30,40,50,60};
int npkArr[] = {10,20,30,40,50};

unsigned long lastSend = 0;

void connectWiFi() {
  WiFi.begin(ssid, password);
  while (WiFi.status() != WL_CONNECTED) delay(300);
}

void connectMQTT() {
  while (!client.connected()) {
    client.connect("ESP32_SIM");
    delay(500);
  }
}

void setup() {
  Serial.begin(115200);
  connectWiFi();
  client.setServer(mqtt_server, mqtt_port);
}

void loop() {
  if (!client.connected()) connectMQTT();
  client.loop();

  if (millis() - lastSend > 5000) {
    lastSend = millis();

    StaticJsonDocument<256> doc;

    doc["device_id"] = "SN_01";
    doc["temp"] = tempArr[random(6)];
    doc["light"] = lightArr[random(5)];
    doc["moisture"] = moistArr[random(4)];
    doc["npk_n"] = npkArr[random(5)];
    doc["npk_p"] = npkArr[random(5)];
    doc["npk_k"] = npkArr[random(5)];
    doc["rssi"] = WiFi.RSSI();

    char buffer[256];
    serializeJson(doc, buffer);

    Serial.println(buffer);
    client.publish("esp32/01/data", buffer);
  }
}
